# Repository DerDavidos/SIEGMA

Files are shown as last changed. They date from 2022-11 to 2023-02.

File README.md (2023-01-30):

# Code

When first loading with CLion only activate one cMake profile for loading everything for the first time.

### Required

    gcc
    arm-non-eabi-gcc
    cMake

### Mac installation process

Install brew: https://brew.sh/index_de, then run:

    brew install gcc-arm-embedded
    brew install cmake

## Troubleshooting

Try with Arduino mega with example code from TMC2209 library each stepper driver

If not working with Arduino, test after taking each of those steps:
    - Check each connection
    - Make sure tx and rx are correct
    - Use different stepper driver
    - Use different cable to computer
    - Replace resistor
    - Try on different computer
    
If it works with the arduino, connections are right, try with pico again, but with commit 208c23bc8ce1775b5c6087e88812553b228f1036
If it works on that commit but not currently the code is probably wrong.
If it does not work on that commit try:
    - Replacing the pico
    - Use different cable to computer
    - Use different computer

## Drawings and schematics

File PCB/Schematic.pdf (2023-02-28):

M1 1 1 2 2 3 3 4 4

# GNDLS³

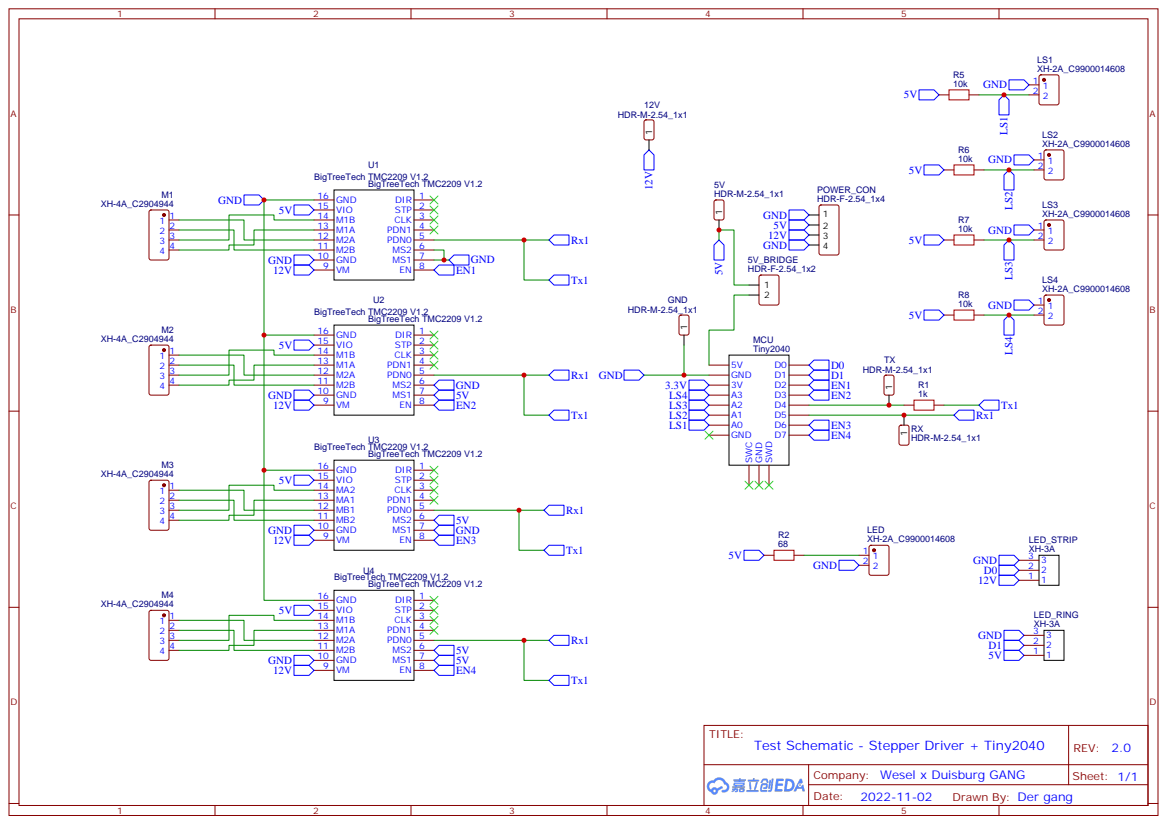
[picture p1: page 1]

Company: Wesel x Duisburg GANG

Drawn By: Der gang

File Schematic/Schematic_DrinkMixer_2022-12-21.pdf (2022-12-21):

M1 1 1 2 2 3 3 4 4

# GNDLS³

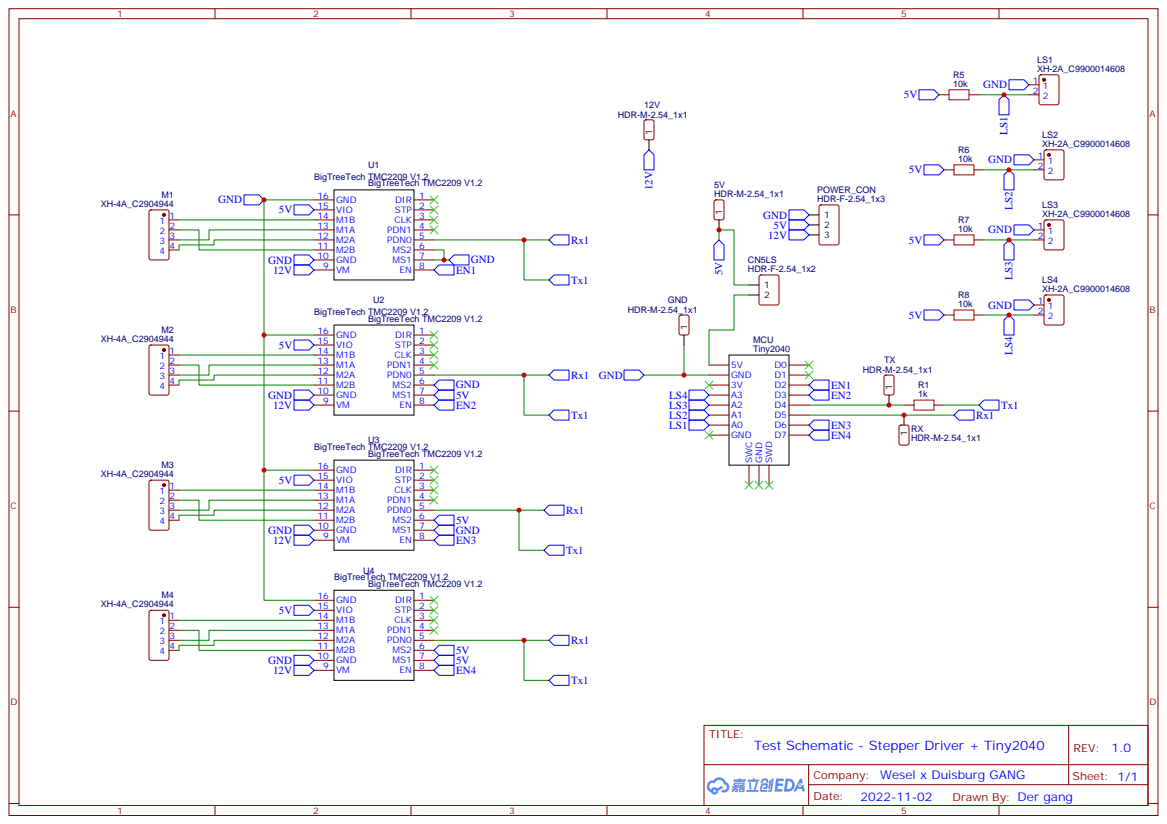
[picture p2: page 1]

Company: Wesel x Duisburg GANG

Drawn By: Der gang

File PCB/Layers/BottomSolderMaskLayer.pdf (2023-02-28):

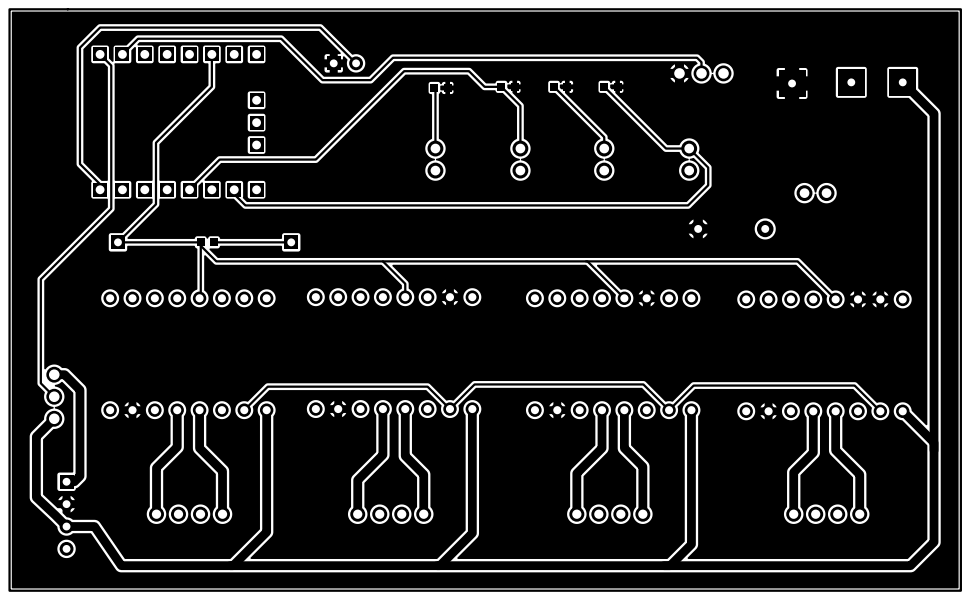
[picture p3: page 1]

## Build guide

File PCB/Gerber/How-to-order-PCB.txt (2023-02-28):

How to Order PCB

Please refer to:
https://docs.easyeda.com/en/PCB/Order-PCB

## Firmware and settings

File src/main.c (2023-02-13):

// Project
#include "dispenser.h"

#ifdef RONDELL
#include "rondell.h"
#endif
// Pico SDK
#include <pico/stdio.h>
#include <pico/time.h>
#include <pico/bootrom.h>
#include <pico/stdio_usb.h>
#include <hardware/watchdog.h>
#include <hardware/adc.h>
// Standard library
#include <stdio.h>
#include <stdlib.h>
#include <string.h>

// maximum count of allowed input length
#define INPUT_BUFFER_LEN 255
// The uart Pins to be used
#define SERIAL_UART SERIAL2

// sequence of allowed character
const char *allowedCharacters = "0123456789i;\nn";
// Array containing the dispenser
Dispenser_t dispenser[NUMBER_OF_DISPENSERS];

// initialize the usb connection to the pico
// @param1 bool if the pico should wait for an usb connection
// @return void
void initPico(bool waitForUSBConnection) {
    if (watchdog_enable_caused_reboot())
        reset_usb_boot(0, 0);

    stdio_init_all(); // init usb
    sleep_ms(2500); // Time to make sure everything is ready

    if (waitForUSBConnection)
        while ((!stdio_usb_connected())); // waits for usb connection
}

// check if the input character is allowed
// @param1 the character to check
// @return true if the input character is in an allowed sequence
bool isAllowedCharacter(uint32_t input) {
    for (uint32_t i = 0; i < strlen(allowedCharacters); ++i) {
        if (input == allowedCharacters[i]) {
            return true;
        }
    }
    return false;
}

// parse a String to fetch the hopper halt timings
// @param1 the received message containing the halt timing
// @return The parsed halt timing as an integer or on failure, a Zero
uint32_t parseInputString(char **message) {
    // every halt timing command has to end with a ';'
    // the function will search for this char and save its position
    char *semicolonPosition = strchr(*message, ';');
    if (semicolonPosition == NULL) {
        return 0; // No Semicolon found
    }
    // the string will be cast, from the beginning of the string to the ';'-Position, into an integer
    uint32_t delay = strtol(*message, &semicolonPosition, 10);
    *message = semicolonPosition + 1;
    return delay;
}

// process the received Message (received over Serial)
// @param1 char buffer containing the received Message
// @return void
void processMessage(char *message) {
    uint16_t dispensersTrigger = 0;

    for (uint8_t i = 0; i < 4; ++i) {
        uint32_t dispenserHaltTimes = parseInputString(&message);
#ifdef RONDELL
        setDispenserHaltTime(&dispenser[0], dispenserHaltTimes);
        if (dispenserHaltTimes > 0) {
            moveToDispenserWithId(i);
            absolute_time_t time = make_timeout_time_ms(DISPENSER_STEP_TIME_MS);
            do {
                sleep_until(time);
                time = make_timeout_time_ms(DISPENSER_STEP_TIME_MS);
                dispenserDoStep(&dispenser[0]);
            } while (!allDispenserInSleepState(dispenser, 1));
        }
#else
        if (dispenserHaltTimes > 0) {
            dispensersTrigger++;
        }
        setDispenserHaltTime(&dispenser[i], dispenserHaltTimes);
#endif
    }

#ifndef RONDELL
    for (int i = 0; i < NUMBER_OF_DISPENSERS; ++i) {
        dispenser[i].othersTriggered = dispensersTrigger;
    }
#endif

#ifndef RONDELL
    absolute_time_t time = make_timeout_time_ms(DISPENSER_STEP_TIME_MS);
    do {
        sleep_until(time);
        time = make_timeout_time_ms(DISPENSER_STEP_TIME_MS);
        // Checks for each dispenser if their next state is reached and perform the according action
        for (uint8_t i = 0; i < NUMBER_OF_DISPENSERS; ++i) {
            dispenserDoStep(&dispenser[i]);
        }
        // When all dispensers are finished, they are in the state sleep
    } while (!allDispenserInSleepState(dispenser, NUMBER_OF_DISPENSERS));
#endif
}

/*
This function's purpose is to establish synchronization between the pico and the pi. The pi sends 'i\n' to the pico
corresponding and to confirm that the string has been received the pico sends back "[POSITION]\n".
This function imprisons the program flow in the while loop until synchronization has been established.
*/
void establishConnectionToMaster(void) {
    uint32_t input_identifier;
    volatile bool identified = false;

    while (!(identified)) {
        input_identifier = getchar_timeout_us(10000000); // 10 seconds wait
        if (input_identifier == 'i') {
            input_identifier = getchar_timeout_us(10000000);
            if (input_identifier == '\n' || input_identifier == 'n') {
#ifdef RONDELL
                printf("RONDELL\n");
#endif
#ifdef LEFT
                printf("LEFT\n");
#endif
#ifdef RIGHT
                printf("RIGHT\n");
#endif
                identified = true;
            }
        } else {
            input_identifier = 0;
            printf("F\n");  // Did not receive proper string; await new string.
        }
    }
}

#ifdef RONDELL
void initialize_adc(uint8_t gpio, uint8_t input) {
    adc_init();
    adc_gpio_init(gpio);
    adc_select_input(input);
}
#endif

// MAIN
int main() {
    initPico(false);

    establishConnectionToMaster();

#ifdef RONDELL
    initialize_adc(28, 2);
    dispenser[0] = createDispenser(0, SERIAL2);
    setUpRondell(2, SERIAL2);
#else
    // create the dispenser with their address and save them in an array
    for (uint8_t i = 0; i < NUMBER_OF_DISPENSERS; ++i) {
        dispenser[i] = createDispenser(i, SERIAL_UART);
    }
#endif

    printf("CALIBRATED\n");
    // Buffer for received Messages
    char *input_buf = malloc(INPUT_BUFFER_LEN);
    memset(input_buf, '\0', INPUT_BUFFER_LEN);
    uint16_t characterCounter = 0;

    // Waits for an input in the form ([0..9];)+[\n|n], each number standing for the wait time of the corresponding dispenser
    while (true) {


        uint32_t input = getchar_timeout_us(10000000); // 10 seconds wait

        if (input == PICO_ERROR_TIMEOUT)
            continue;

        // ignore the received character if it is not an allowed one
        if (!isAllowedCharacter(input)) {
#ifdef DEBUG
            printf("Received '%c' which is not allowed\n", input);
#endif
            continue;
        }


        // received end character, message should be complete, start with processing
        if (input == 'n' || input == '\n') {
#ifdef DEBUG
            printf("Process Msg len: %d\n", characterCounter);
#endif
            processMessage(input_buf);
            memset(input_buf, '\0', INPUT_BUFFER_LEN);
            characterCounter = 0;
            printf("READY\n");
        }
            // received to many characters -> flushing the uart connection and start over
        else if (characterCounter >= INPUT_BUFFER_LEN - 1) {
#ifdef DEBUG
            printf("Input too long, flushing...\n");
#endif
            memset(input_buf, '\0', INPUT_BUFFER_LEN);
            characterCounter = 0;
        }
            // character is allowed and we did not reach the end
        else {
#ifdef DEBUG
            printf("Received: %c (counter: %d)\n", input, characterCounter);
#endif
            input_buf[characterCounter] = input;
            ++characterCounter;
        }
    }
}

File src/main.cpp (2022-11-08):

#include <cstdio>
#include "pico/stdio.h"
#include "pico/stdio_usb.h"
#include "pico/time.h"
#include "hardware/uart.h"

#include "TMC2209.h"
#include "hardware/watchdog.h"
#include "pico/bootrom.h"

#define SERIAL_BAUD_RATE 115200

extern "C" {
#include "SerialUART.h"
}

int main() {

    if (watchdog_enable_caused_reboot()) {
        reset_usb_boot(0, 0);
    }

    // init usb
    stdio_init_all();

    // waits for usb connection, REMOVE to continue without waiting for connection
    while ((!stdio_usb_connected()));

    sleep_ms(100);
    printf("Connected\n");
    sleep_ms(1000);
    SerialUART(uart0, PIN_SERIAL1_TX, PIN_SERIAL1_RX);

    printf("UART\n");

    TMC2209 tmc;
    tmc.setup(SERIAL_BAUD_RATE);
    printf("Setup: TMC2209 setup done.\n");

    while (!tmc.isSetupAndCommunicating()) {
        printf("Setup: Stepper driver NOT setup and communicating!\n");
        sleep_ms(1000);
        tmc.setup(SERIAL_BAUD_RATE);
    }
    printf("Setup: Stepper driver setup and communicating!\n");

    tmc.setRunCurrent(100);
    tmc.enable();

    while (1) {
        while (!tmc.isSetupAndCommunicating()) {
            printf("Stepper driver NOT setup and communicating!\n");
            sleep_ms(1000);
        }
        tmc.moveAtVelocity(0);
        sleep_ms(1000);
        tmc.moveAtVelocity(50000);
        sleep_ms(1000);
    }

    return 0;
}

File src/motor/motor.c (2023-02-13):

#include "motor.h"

#include <pico/time.h>
#include <hardware/gpio.h>

#include <stdio.h>

void setUpEnablePin(Motor_t *motor, SerialAddress_t id) {
    switch (id) {
        case 0:
            motor->enablePin = MOTOR_ENABLE_PINT_0;
            break;
        case 1:
            motor->enablePin = MOTOR_ENABLE_PINT_1;
            break;
        case 2:
            motor->enablePin = MOTOR_ENABLE_PINT_2;
            break;
        case 3:
            motor->enablePin = MOTOR_ENABLE_PINT_3;
            break;
        default:
            motor->enablePin = 0;
    }
    gpio_init( motor->enablePin);
    gpio_set_dir( motor->enablePin, GPIO_OUT);
}

void setUpMotor(Motor_t *motor, SerialAddress_t address, SerialUART_t uart) {
    setUpEnablePin(motor, address);
    disableMotorByPin(motor);

    TMC2209_setup(&motor->tmc2209, uart, SERIAL_BAUD_RATE, address);

    while (!TMC2209_isSetupAndCommunicating(&motor->tmc2209)) {
#ifdef DEBUG
        if (TMC2209_disabledByInputPin(&motor->tmc2209)) {
            printf("Setup: Stepper driver with address %i DISABLED by input pin!\n", address);
        }
        printf("Setup: Stepper driver with address %i NOT communicating and setup!\n", address);
#endif

        TMC2209_setup(&motor->tmc2209, uart, SERIAL_BAUD_RATE, address);
        sleep_ms(500);
    }

#ifdef DEBUG
    printf("Setup: Stepper driver with address %i communicating and setup!\n", address);
#endif

    TMC2209_setRunCurrent(&motor->tmc2209, 100);
    TMC2209_setHoldCurrent(&motor->tmc2209, 50);
    TMC2209_enable(&motor->tmc2209);

    motor->direction = DIRECTION_UP;
}

bool motorIsCommunicating(Motor_t *motor) {
    return TMC2209_isSetupAndCommunicating(&motor->tmc2209);
}

void enableMotorByPin(Motor_t *motor) {
    gpio_pull_down(motor->enablePin);
}

void disableMotorByPin(Motor_t *motor) {
    gpio_pull_up(motor->enablePin);
}

Motor_t createMotor(SerialAddress_t address, SerialUART_t uart) {
    Motor_t motor = {.address = address};
    setUpMotor(&motor, address, uart);
    return motor;
}

void moveMotorUp(Motor_t *motor) {
    TMC2209_moveAtVelocity(&motor->tmc2209, motor->direction * MOTOR_SPEED);
    TMC2209_moveAtVelocity(&motor->tmc2209, motor->direction * MOTOR_SPEED);
}

void moveMotorDown(Motor_t *motor) {
    TMC2209_moveAtVelocity(&motor->tmc2209, motor->direction * -MOTOR_SPEED);
    TMC2209_moveAtVelocity(&motor->tmc2209, motor->direction * -MOTOR_SPEED);
}

void stopMotor(Motor_t *motor) {
    TMC2209_moveAtVelocity(&motor->tmc2209, 0);
    TMC2209_moveAtVelocity(&motor->tmc2209, 0);
}

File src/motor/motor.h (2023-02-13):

#ifndef SIEGMA_MOTOR_H
#define SIEGMA_MOTOR_H

#include "serialUART.h"
#include "tmc2209.h"

#include <stdint.h>

#define MOTOR_ENABLE_PINT_0 2
#define MOTOR_ENABLE_PINT_1 3
#define MOTOR_ENABLE_PINT_2 6
#define MOTOR_ENABLE_PINT_3 7

#define MOTOR_SPEED 50000

#define DIRECTION_UP 1
#define DIRECTION_DOWN (-1)

// struct containing information (pins, stepper driver, direction, Serial address) for a motor
typedef struct Motor {
    uint8_t enablePin;
    TMC2209_t tmc2209;
    SerialAddress_t address;
    int direction;
} Motor_t;

// initializes a new motor
// @param1 The new initialized motor
// @param2 Serial address of the motor (for more information: https://github.com/janelia-arduino/TMC2209)
// @param3 Uart pins to be used
// @return void
void setUpMotor(Motor_t *motor, SerialAddress_t address, SerialUART_t uart);

// Enable the motor
// @param1 motor to be enabled
// @return void
void enableMotorByPin(Motor_t *motor);

// Disable the motor
// @param1 motor to be disabled
// @return void
void disableMotorByPin(Motor_t *motor);

// Move the motor up
// @param1 motor to be moved
// @return void
void moveMotorUp(Motor_t *motor);

// Move the motor down
// @param1 motor to be moved
// @return void
void moveMotorDown(Motor_t *motor);

// Stop the motor
// @param1 motor to be stopped
// @return void
void stopMotor(Motor_t *motor);

// Create a new motor and initialize its pins
// @param1 Serial address of the stepper driver (for more information: https://github.com/janelia-arduino/TMC2209)
// @param2 Uart pins to be used
// @return Motor struct of the new motor
Motor_t createMotor(SerialAddress_t address, SerialUART_t uart);

// Check if the motor is capable of communication over uart
// @param1 Motor to be checked
// @return true if the motor communicates, otherwise false
bool motorIsCommunicating(Motor_t *motor);

#endif //SIEGMA_MOTOR_H

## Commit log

2022-11-08 uart in c
2022-12-03 dispenser and touch sensor lib
2022-12-05 serial uart para
2022-12-21 Add files via upload
    Die Gerber Files der bestellten PCB
2022-12-21 Add files via upload
    Kann die alte nicht löschen. Das hier ist aber die Neue
2022-12-26 create motor library and dispenser states
2022-12-26 limit Switch struct
2023-01-09 enable/disable motors by pin
2023-01-17 state pattern/enable pin
2023-01-26 fixed limit switch pin
    [limitSwitch.h, main.c, rondell.c]
2023-01-27 adapted rondell to new ldr voltage level and new led resistor
2023-01-27 fixed values so that dispensers and hoppers align better
    [main.c, rondell.c]
2023-01-28 fixed a logical mistake
    [rondell.c]
2023-02-01 Working Rondell Version -> a value needed to be fixed
    [rondell.c]
2023-02-03 fix find direction of dispenser
    [dispenser.c]
2023-02-03 fixed a bug that prevented transition from dispenser n to n-1
    [rondell.c]
2023-02-06 fixed a minor mistake and improved alignment. New function to reset when lightning changes
    [main.c, rondell.c]
2023-02-11 new limit switch gpios
2023-02-12 set hold current
2023-02-13 added comments for motor.h and dispenser.h
2023-02-14 fixed a grammar mistake in comment
    [rondell.c]
2023-02-28 update pcb schematic
    [Drill_PTH_Through.DRL, Drill_PTH_Through_Via.DRL, Gerber_BoardOutlineLayer.GKO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]
